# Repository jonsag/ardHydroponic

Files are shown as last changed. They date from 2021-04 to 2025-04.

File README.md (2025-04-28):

# ardHydroponic

An Arduino Mega managing a hydroponic plant bed.  

Visualization on an LCD screen  
Managed and configured with push buttons  
Data uploaded to Blynk app and ThingSpeak  
Monitored on a webpage

## Hardware

Things marked as optional are used when you make a PCB and/or an ESP-01 module.  

1 x Arduino Mega 2560, [AliExpress](https://www.aliexpress.com/wholesale?SearchText=arduino+mega+2560)  

1 x LCD display, 4x20 with I2C communication, [AliExpress](https://www.aliexpress.com/wholesale?SearchText=lcd+4x20+i2c)  

1 x ESP-01 module, [AliExpress](https://www.aliexpress.com/wholesale?SearchText=esp-01) (optional)  

5 x Momentary push button [AliExpress](https://www.aliexpress.com/wholesale?SearchText=switch+dip+6mm)  

5 x MOSFET module, [AliExpress](https://www.aliexpress.com/wholesale?SearchText=mosfet+module+irf520)  

4 x pump, [AliExpress](https://www.aliexpress.com/wholesale?SearchText=peristaltic+pump)  

1 x magnetic stirrer, [DIY suggestion](https://www.instructables.com/How-to-Make-a-Cheap-Portable-Magnetic-Stirrer/)  

1 x EC/TDS sensor, [AliExpress](https://www.aliexpress.com/wholesale?SearchText=dfrobot+gravity+tds)  

1 x pH sensor, [AliExpress](https://www.aliexpress.com/wholesale?SearchText=dfrobot+gravity+ph)  

1 x DS18B20 temperature sensor, [AliExpress](https://www.aliexpress.com/wholesale?SearchText=ds18b20)  

1 x KY-019 relay module, [AliExpress](https://www.aliexpress.com/wholesale?SearchText=ky-019) (optional)  

5 x 10 kohm resistor  

1 x 4.7 kohm resistor  

1 x 1 kohm resistor (optional)  

1 x 2.2 kohm resistor (optional)  

1 x 2 pole screw terminal block, 5.0mm leg space [AliExpress](https://www.aliexpress.com/wholesale?SearchText=screw+terminal+block+5.0+mm) (optional)  

1 x 3 pole screw terminal block, 5.0mm leg space [AliExpress](https://www.aliexpress.com/wholesale?SearchText=screw+terminal+block+5.0+mm) (optional)  

1 x 5 pole screw terminal block, 5.0mm leg space [AliExpress](https://www.aliexpress.com/wholesale?SearchText=screw+terminal+block+5.0+mm) (optional)  

1 x 6 pole screw terminal block, 5.0mm leg space [AliExpress](https://www.aliexpress.com/wholesale?SearchText=screw+terminal+block+5.0+mm) (optional)  

1 x 4x2 pin socket header (optional)  

Some single row pin and socket headers, 100mil legs space (optional)  

1 x DC power source, same voltage as your pumps. If this will also feed the Arduino board, not higher than 12V  

A PCB like the one in [this gerber zip](KiCAD/ardHydroponic/Gerber/ardHydroponic.zip) (optional)  

Connect and build everything according to the [schematics](KiCAD/ardHydroponic/ardHydroponic.pdf) in KiCAD.  

Calibration fluids:  
pH: two solutions with known values, for example 4.00 and 7.00  (other values will also work)  
TDS: solution with known TDS value  

## Usage

Your setup will have five push buttons and one LCD display.  
Everything is monitored and adjusted from the LCD.  
A lot of output is also provided on the serial output from the Mega.  

### Modes

There are four major modes of the system:  

* Running...  
* Maintenance  
* Settings  
* Special  

Also there is a 'Reading...' mode that the system enters when measuring in 'Running...' mode, and an 'Uploading...' mode when uploading data to internet.  

You advance from one mode to the next by pushing and holding down 'Button 1' for one second.  
When you do this in 'Special' mode you loop back to 'Running...' mode again.  

### 'Running...' mode

Button number:  

1. Enter next mode  
   * Long press: enter next mode  
2. No function  
3. No function  
4. No function  
5. No function  

LCD shows measured values, and whether they're too low or too high  

### 'Maintenance' mode

Button number:  

1. Enter next mode/Toggle output
   * Long press: enter next mode  
   * Short press: start or stop the indicated output  
2. Select previous output
3. Select next output
4. No function
5. No function

LCD shows selected output  

### 'Settings' mode

Button number:  

1. Enter next mode/Save variable  
   * Long press: leave this mode and enter next  
   * Short press: save variable to EEPROM  
2. Select previous variable
3. Select next variable
4. Step down selected variable
5. Step up selected variable

There are seventeen variables available:

* Nutr pump time,   ms
* pH+ pump time,    ms
* pH- pump time,    ms
* Clean pumps time, ms
* Iteration time,   ms
* Stir time,        ms
* Stir interval,    ms
* pH low,           pH
* pH high,          pH
* TDS low,         ppm
* k value,    constant
* TDS factor, constant
* Neutral pH,       pH
* Acid pH,          pH
* Neutral voltage,  mV
* Acid voltage,     mV
* pH voltage offs., mV

The names are pretty self explanatory.  
However, the last seven of these will be further explained in the calibration section below.  

The second line on the LCD will show the variable name.  
Line three will show the value stored in EEPROM.  
Line four will show the new value you step up and down.  

Also lines three and four will show pH and TDS when applicable.  

There is some sanity checking done of these variables when changing them via the LCD, but beware of what you tap in.  

### 'Special' mode

Button number:  

1. Enter next mode/Run action  
   * Long press: leave this mode and enter next  
   * Short press: Run selected action  
2. Select previous action
3. Select next action
4. No function
5. No function

LCD shows selected action and action result  

#### Actions

* Interact with ESP module in serial monitor
* Clear EEPROM. On next restart the EEPROM will be rewritten with the default values from config
* Reset ESP module
* Reset whole system
* Toggle the serial debugging output. Will go back to the setting in config.h after a restart.
* Print the IP of the ESP module
* Print MAC address of the ESP module

## Calibration

### TDS value

Put the TDS sensor in a solution with a know TDS value.  

Enter 'Settings' mode.

Select the 'TDS factor' variable using 'Button 2' and 'Button 3'.  
Enter the TDS factor of your known solution using 'Button 4' and 'Button 5'.  
The TDS value on the left of the screen will be updated whenever you push those buttons.  
Save the new 'TDS factor' with a short press on 'Button 1'.  

Select the 'k value' variable using 'Button 2' and 'Button 3'.  
Step up and down 'k value' using 'Button 4' and 'Button 5'.  
The TDS value on the left of the screen will be updated whenever you push those buttons.  
When the TDS value shown on screen correlates with your known solution save the 'k value' with a short press on 'Button 1'.  

### pH value

Enter 'Settings' mode.  

Select the 'Neutral pH' variable using 'Button 2' and 'Button 3'.  
Enter the pH value of your known solution, ie the one with the higher pH, using 'Button 4' and 'Button 5'.  
Save the new value with a short press on 'Button 1'.  

Select the 'Acid pH' variable using 'Button 2' and 'Button 3'.  
Enter the pH value of your known solution, ie the one with the lower pH, using 'Button 4' and 'Button 5'.  
Save the new value with a short press on 'Button 1'.  

Put your pH sensor in the neutral solution.  
Select the 'Neutral voltage' variable using 'Button 2' and 'Button 3'.  
On the lower right of the screen you will now see the measured voltage from the pH sensor in millivolts. You can't change that. However, pressing 'Button 4' or 'Button 5' will update that measurement.  
When you get a solid reading, save the value with a short press on 'Button 1'.  

Put your pH sensor in the acid solution.  
Select the 'Acid voltage' variable using 'Button 2' and 'Button 3'.  
On the lower right of the screen you will now see the measured voltage from the pH sensor in millivolts. You can't change that. However, pressing 'Button 4' or 'Button 5' will update that measurement.  
When you get a solid reading, save the value with a short press on 'Button 1'.  

There is also a 'pH voltage offset' for further trimming.  

## Web interface

A simple web page shows last data read and ThingSpeak upload status.  

You can also disable an enable the outputs relay from the page.

You can find the IP address of the web server using the 'Special' mode.  

## Blynk app

The app shows latest values of the sensors.  

Also you can control the outputs relay from it.  

## Software configuration

All configuration is made in 'config.h'

The most interesting variables are:

### varNames

If you want it in your own language, change it here.  
Other LCD output is mostly found in 'LCD.h', but also in some other places. Sorry...  

### vars

These are the start values of the variables that can be edited from the LCD.  
If you change these after having having uploaded the sketch once, it will not be used since these are now read from EEPROM.  

### incs

The increments/decrements of the variables above.  
(How big should the jumps be when using buttons 'Button 4' and 'Button5'.)  

## Libraries and boards in Arduino IDE

Most can be installed from within the Arduino IDE, but look out for the liquid crystal library so you don't install the wrong one.  
Read below!  

### ESP8266 board library

Add [http://arduino.esp8266.com/stable/package_esp8266com_index.json](http://arduino.esp8266.com/stable/package_esp8266com_index.json) (as a text line), in Files->Preferences->Additional Boards Manager URLs:  

Then go to Tools->Board:...->Boards Manager...,search for esp8266 and install it.  

### LiquidCrystal_I2C

Don't install the LiquidCrystal_I2C library with Arduino IDE's library manager.  

Instead use the one from [https://github.com/fdebrabander/Arduino-LiquidCrystal-I2C-library](https://github.com/fdebrabander/Arduino-LiquidCrystal-I2C-library).  

### FTDebouncer

[https://github.com/ubidefeo/FTDebouncer](https://github.com/ubidefeo/FTDebouncer)  

### Blynk

[https://github.com/blynkkk/blynk-library](https://github.com/blynkkk/blynk-library)  

### ThingSpeak

[https://github.com/iobridge/thingspeak](https://github.com/iobridge/thingspeak)  

### NTPClient

[https://github.com/arduino-libraries/NTPClient](https://github.com/arduino-libraries/NTPClient)  

## Install and configure

### Create accounts for online visualizations

#### thingspeak

Get an account at [thingspeak.com](https://thingspeak.com).

Create a new channel with the fields:

* Field1: Temp
* Field2: pH
* Field3: TDS

Take note of your channel ID and write API key.  

#### blynk

Download [Blynk](https://play.google.com/store/apps/details?id=cc.blynk) to your phone.  

Open Blynk and create a new project.  

Add widget boxes:  

* Gauge, Temperature, Input: Virtual V0, scaled 0-30
* Gauge, pH, Input: Virtual V1, scaled 0-15
* Gauge, TDS, Input Virtual V2, scaled 0-4000
* Button, Enabled, Mode: Switch, Output: Virtual V3

In your mail you will have received the authorization token.  

### Arduino Mega

Compile and upload hydroponicBase/src/* with, for example, Platform IO.  

When uploading over USB you must open up the connection between D14 and RESET, ie remove the jumper JP1.

### ESP-01

Rename/copy hydroponicConnect/src/secrets.h.template to hydroponicConnect/src/secrets.h, and edit it with your own values/keys.  

Compile and upload hydroponicConnect/src/* with, for example, Platform IO.  

## Trouble shooting

### Resetting EEPROM to default values at every start

Edit ardHydroponic.ino  

Uncomment the line  

    //clearEEPROM();

and upload sketch.  

## Misc

### Useful programs

#### cu

A simple serial monitor  

Get serial output  
>$ cu -l /dev/ttyACM0 -s 9600

Exit with ~. (tilde dot)  

#### picocom

A more versatile serial monitor  

Get serial output  
>$ picocom -b 115200 /dev/ttyACM0 --omap crcrlf

Exit with Ctrl+a Ctrl+x  

### Links

EC sensor:  
[https://wiki.dfrobot.com/Gravity__Analog_TDS_Sensor___Meter_For_Arduino_SKU__SEN0244](https://wiki.dfrobot.com/Gravity__Analog_TDS_Sensor___Meter_For_Arduino_SKU__SEN0244)  

pH sensor:  
[https://wiki.dfrobot.com/Gravity__Analog_pH_Sensor_Meter_Kit_V2_SKU_SEN0161-V2](https://wiki.dfrobot.com/Gravity__Analog_pH_Sensor_Meter_Kit_V2_SKU_SEN0161-V2)  

### Screen shots

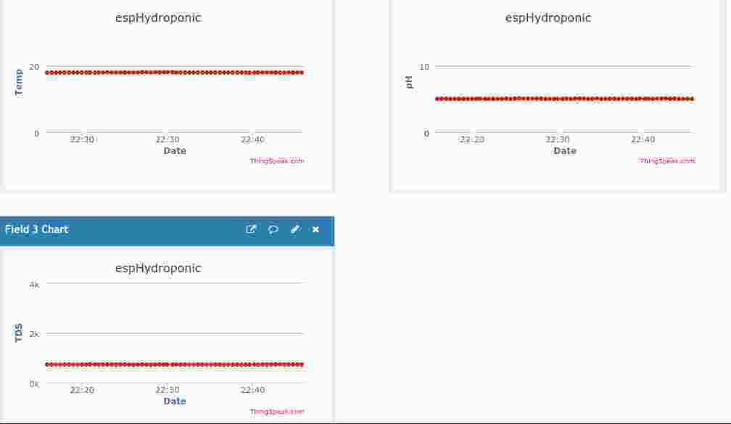
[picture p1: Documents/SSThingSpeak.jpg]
ThingSpeak
  
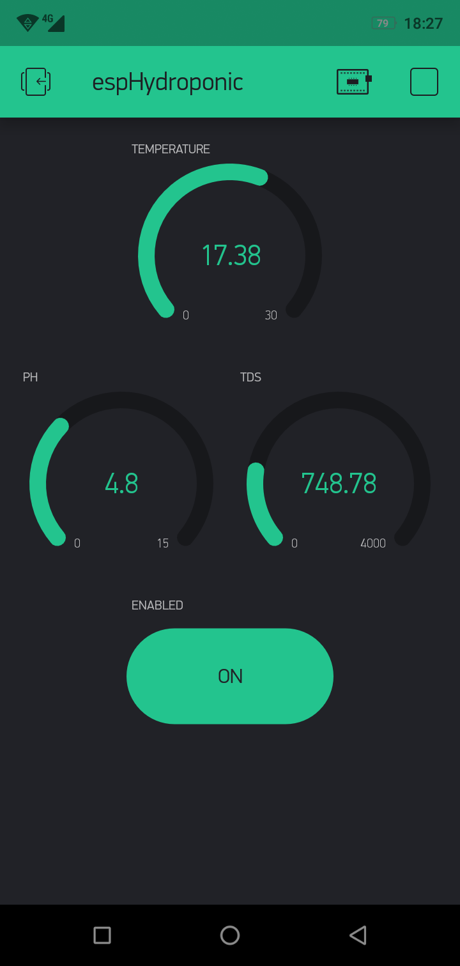
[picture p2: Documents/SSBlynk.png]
Blynk
  
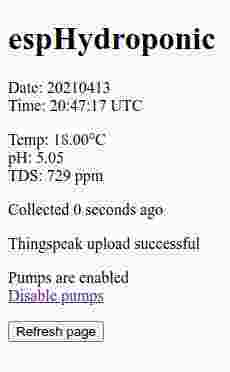
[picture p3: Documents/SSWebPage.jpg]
Web interface


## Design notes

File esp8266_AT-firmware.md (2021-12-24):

# espLogger

An ESP-01 module to handle logging and monitoring of the ardHydroponic.  

## Check firmware version

Hook up your FTDI device to the ESP module.  

    FTDI            ESP-01  
    1 GND   ->      2   GND
    2 CTS   ->
    3 VCC   ->      7   VCC
    4 Tx    ->      8   Rx
    5 Rx    ->      1   Tx
    6 DTR   ->

Check connection with picocom  
>$ picocom -b 115200 /dev/ttyUSB0 --omap crcrlf  

    picocom v2.2

    port is        : /dev/ttyUSB0
    flowcontrol    : none
    baudrate is    : 115200
    parity is      : none
    databits are   : 8
    stopbits are   : 1
    escape is      : C-a
    local echo is  : no
    noinit is      : no
    noreset is     : no
    nolock is      : no
    send_cmd is    : sz -vv
    receive_cmd is : rz -vv -E
    imap is        : 
    omap is        : crcrlf,
    emap is        : crcrlf,delbs,

    Type [C-a] [C-h] to see available commands

    Terminal ready

Check if the ESP is answering  
>AT

    OK  

Check fw version  
>AT+GMR

    AT version:0.25.0.0(Jun  5 2015 16:27:16)
    SDK version:1.1.1
    Ai-Thinker Technology Co. Ltd.
    Jun 23 2015 23:23:50

    OK

Exit program  
>$ Ctrl+a Ctrl+x  

## Update firmware

Install tool  
>$ pip install esptool

Pull GPIO0 to ground and start the ESP via the FTDI.  
Also make sure you got a solid 3.3V source as the chip will not boot properly otherwise.  

### Source from aprbrother  

Download firmware from [http://wiki.aprbrother.com/wiki/Firmware_For_ESP8266](http://wiki.aprbrother.com/wiki/Firmware_For_ESP8266).  
>$ wget https://i1.aprbrother.com/ai-thinker-v1.1.1.bin  

Flash firmware  
>$ esptool.py -p /dev/ttyUSB0 -b 115000 write_flash 0x000000 ai-thinker-v1.1.1.bin  

    esptool.py v3.0
    Serial port /dev/ttyUSB0
    Connecting....
    Detecting chip type... ESP8266
    Chip is ESP8266EX
    Features: WiFi
    Crystal is 26MHz
    MAC: e8:db:84:dc:4e:77
    Uploading stub...
    Running stub...
    Stub running...
    Configuring flash size...
    Compressed 1044480 bytes to 204643...
    Wrote 1044480 bytes (204643 compressed) at 0x00000000 in 18.2 seconds (effective 459.2 kbit/s)...
    Hash of data verified.

    Leaving...
    Hard resetting via RTS pin...

### Get AT sources from EspressIF

[https://www.espressif.com/en/support/download/at?keys=&field_type_tid%5B%5D=799](https://www.espressif.com/en/support/download/at?keys=&field_type_tid%5B%5D=799)  

Look for ESP8266 NonOS AT Bin, download and extract it  

### Source from espressif, ESP8266 NonOS AT Bin v1.7.4  
  
>$ wget https://www.espressif.com/sites/default/files/ap/ESP8266_NonOS_AT_Bin_V1.7.4.zip  
>$ unzip ESP8266_NonOS_AT_Bin_V1.7.4.zip  
>$ cd ESP8266_NonOS_AT_Bin_V1.7.4/bin/  

Find out how to upload it  
>$ cat at/README.md

    ...
    ### Flash size 8Mbit: 512KB+512KB
        boot_v1.2+.bin              0x00000
        user1.1024.new.2.bin        0x01000
        esp_init_data_default.bin   0xfc000
        blank.bin                   0x7e000 & 0xfe000
    ...

Flash chip  
>$ esptool.py -p /dev/ttyUSB0 -b 74880 write_flash --flash_size 1MB --flash_freq 26m 0x00000 boot_v1.7.bin 0x01000 at/512+512/user1.1024.new.2.bin 0xFC000 esp_init_data_default_v08.bin 0x7E000 blank.bin 0xFE000 blank.bin

Or with fewer options  
>$ esptool.py -p /dev/ttyUSB0 write_flash 0x00000 boot_v1.7.bin 0x01000 at/512+512/user1.1024.new.2.bin 0xFC000 esp_init_data_default_v08.bin 0x7E000 blank.bin 0xFE000 blank.bin  

    esptool.py v3.0
    Serial port /dev/ttyUSB0
    Connecting....
    Detecting chip type... ESP8266
    Chip is ESP8266EX
    Features: WiFi
    Crystal is 26MHz
    MAC: e8:db:84:dc:4e:77
    Uploading stub...
    Running stub...
    Stub running...
    Configuring flash size...
    Compressed 4080 bytes to 2936...
    Wrote 4080 bytes (2936 compressed) at 0x00000000 in 0.4 seconds (effective 78.4 kbit/s)...
    Hash of data verified.
    Compressed 413444 bytes to 296966...
    Wrote 413444 bytes (296966 compressed) at 0x00001000 in 40.4 seconds (effective 81.8 kbit/s)...
    Hash of data verified.
    Compressed 128 bytes to 75...
    Wrote 128 bytes (75 compressed) at 0x000fc000 in 0.0 seconds (effective 32.0 kbit/s)...
    Hash of data verified.
    Compressed 4096 bytes to 26...
    Wrote 4096 bytes (26 compressed) at 0x0007e000 in 0.0 seconds (effective 2052.6 kbit/s)...
    Hash of data verified.
    Compressed 4096 bytes to 26...
    Wrote 4096 bytes (26 compressed) at 0x000fe000 in 0.0 seconds (effective 2034.8 kbit/s)...
    Hash of data verified.

    Leaving...
    Hard resetting via RTS pin...

Firmware check in serial monitor  
>AT+GMR

    AT version:1.7.4.0(May 11 2020 19:13:04)
    SDK version:3.0.4(9532ceb)
    compile time:May 27 2020 10:12:17
    Bin version(Wroom 02):1.7.4
    OK

### Source from espressif, ESP8266 NonOS AT Bin v1.6.2  

Get source  
>$ wget wget https://www.espressif.com/sites/default/files/ap/ESP8266_AT_Bin_V1.6.2_0.zip  
>$ unzip ESP8266_AT_Bin_V1.6.2_0.zip  
>$ cd ESP8266_AT_Bin_V1.6.2/bin/  

Find out how to upload it  
>$ cat at/README.md

    ...
    ### Flash size 8Mbit: 512KB+512KB
        boot_v1.2+.bin              0x00000
        user1.1024.new.2.bin        0x01000
        esp_init_data_default.bin   0xfc000 (optional)
        blank.bin                   0x7e000 & 0xfe000
    ...

Flash chip  
>$ esptool.py -p /dev/ttyUSB0 -b 74880 write_flash --flash_size 1MB --flash_freq 26m 0x00000 boot_v1.7.bin 0x01000 at/512+512/user1.1024.new.2.bin 0xFC000 esp_init_data_default_v08.bin 0x7E000 blank.bin 0xFE000 blank.bin

    esptool.py v3.0
    Serial port /dev/ttyUSB0
    Connecting....
    Detecting chip type... ESP8266
    Chip is ESP8266EX
    Features: WiFi
    Crystal is 26MHz
    MAC: e8:db:84:dc:4e:77
    Uploading stub...
    Running stub...
    Stub running...
    Configuring flash size...
    Compressed 4080 bytes to 2936...
    Wrote 4080 bytes (2936 compressed) at 0x00000000 in 0.4 seconds (effective 78.3 kbit/s)...
    Hash of data verified.
    Compressed 408388 bytes to 293527...
    Wrote 408388 bytes (293527 compressed) at 0x00001000 in 40.1 seconds (effective 81.5 kbit/s)...
    Hash of data verified.
    Compressed 128 bytes to 75...
    Wrote 128 bytes (75 compressed) at 0x000fc000 in 0.0 seconds (effective 32.6 kbit/s)...
    Hash of data verified.
    Compressed 4096 bytes to 26...
    Wrote 4096 bytes (26 compressed) at 0x0007e000 in 0.0 seconds (effective 2048.4 kbit/s)...
    Hash of data verified.
    Compressed 4096 bytes to 26...
    Wrote 4096 bytes (26 compressed) at 0x000fe000 in 0.0 seconds (effective 2175.0 kbit/s)...
    Hash of data verified.

    Leaving...
    Hard resetting via RTS pin...

Firmware check in serial monitor  
>AT+GMR

    AT version:1.6.2.0(Apr 13 2018 11:10:59)
    SDK version:2.2.1(6ab97e9)
    compile time:Jun  7 2018 19:34:26
    Bin version(Wroom 02):1.6.2
    OK

### Source from espressif, ESP8266 NonOS AT Bin v1.5.1  

Get source  
>$ wget wget https://www.espressif.com/sites/default/files/ap/esp8266_at_bin_v1.5.1.zip  
>$ unzip esp8266_at_bin_v1.5.1.zip  
>$ cd ESP8266_AT_Bin_V1.5.1/bin  

Find out how to upload it  
>$ cat at/README.md

    ...
    ### Flash size 8Mbit: 512KB+512KB
        boot_v1.2+.bin              0x00000
        user1.1024.new.2.bin        0x01000
        esp_init_data_default.bin   0xfc000 (optional)
        blank.bin                   0x7e000 & 0xfe000
    ...

Flash chip  
>$ esptool.py -p /dev/ttyUSB0 -b 74880 write_flash --flash_size 1MB --flash_freq 26m 0x00000 boot_v1.7.bin 0x01000 at/512+512/user1.1024.new.2.bin 0xfc000 esp_init_data_default.bin 0x7E000 blank.bin 0xFE000 blank.bin

    esptool.py v3.0
    Serial port /dev/ttyUSB0
    Connecting....
    Detecting chip type... ESP8266
    Chip is ESP8266EX
    Features: WiFi
    Crystal is 26MHz
    MAC: e8:db:84:dc:4e:77
    Uploading stub...
    Running stub...
    Stub running...
    Configuring flash size...
    Compressed 4080 bytes to 2936...
    Wrote 4080 bytes (2936 compressed) at 0x00000000 in 0.4 seconds (effective 78.3 kbit/s)...
    Hash of data verified.
    Compressed 427044 bytes to 305765...
    Wrote 427044 bytes (305765 compressed) at 0x00001000 in 41.6 seconds (effective 82.1 kbit/s)...
    Hash of data verified.
    Compressed 128 bytes to 75...
    Wrote 128 bytes (75 compressed) at 0x000fc000 in 0.0 seconds (effective 32.0 kbit/s)...
    Hash of data verified.
    Compressed 4096 bytes to 26...
    Wrote 4096 bytes (26 compressed) at 0x0007e000 in 0.0 seconds (effective 2153.5 kbit/s)...
    Hash of data verified.
    Compressed 4096 bytes to 26...
    Wrote 4096 bytes (26 compressed) at 0x000fe000 in 0.0 seconds (effective 2133.6 kbit/s)...
    Hash of data verified.

    Leaving...
    Hard resetting via RTS pin...

Firmware check in serial monitor  
>AT+GMR

    AT version:1.5.0.0(Oct 24 2017 12:03:18)
    SDK version:2.1.0(ace2d95)
    compile time:Oct 24 2017 15:48:02
    Bin version(Wroom 02):1.5.1
    OK

### After upload

Remove the ground connection on GPIO0 and boot up and connect again  
>$ picocom -b 115200 /dev/ttyUSB0 --omap crcrlf  

## AT commands

Check firmware version  
>AT+GMR  

    AT version:1.3.0.0(Jul 14 2016 18:54:01)
    SDK version:2.0.0(5a875ba)
    v1.0.0.3
    Mar 13 2018 09:35:47
    OK

Check WiFi mode  
>AT+CWMODE?  

    +CWMODE:0

    OK

Set as station  
>AT+CWMODE=1

    OK

Mode 1 -> STA (station)  
Mode 2 -> AP (access point)  
Mode 3 -> Both

Search for access points  
>AT+CWLAP

    +CWLAP:(0,"ESP-E0569F",-56,"52:02:91:e0:56:9f",11)
    +CWLAP:(2,"tureborg2",-55,"00:1b:2f:50:e6:16",11)

    OK

Connect to access point  
>AT+CWJAP="\<access point>","\<password>"  

    WIFI CONNECTED
    WIFI GOT IP

    OK

Show IP-address
>AT+CIFSR

    +CIFSR:APIP,"192.168.4.1"
    +CIFSR:APMAC,"ea:db:84:dc:4e:77"
    +CIFSR:STAIP,"192.168.10.78"
    +CIFSR:STAMAC,"e8:db:84:dc:4e:77"

    OK

Disconnect from access point
>AT+CWQAP

    WIFI DISCONNECT

    OK

Set serial speed  
>AT+CIOBAUD=9600

    OK

Permanently set serial speed, for example, 9600 baud / 8 data bits / 1 stop bits and none parity and flow control  
>AT+UART_DEF=9600,8,1,0,0

Reset  
>AT+RST

    OK
    WIFI DISCONNECT
    ...
    Ai-Thinker Technology Co. Ltd.

    invalid
    WIFI CONNECTED
    WIFI GOT IP

## esptool.py

When using esptool you must pull GPIO0 to GND  

Allowed baud rates:  
74880, 115200, 230400, 460800, 921600, 1500000, >1500000

Read MAC address  
>$ esptool.py -p /dev/ttyUSB0 read_mac

    esptool.py v3.0
    Serial port /dev/ttyUSB0
    Connecting....
    Detecting chip type... ESP8266
    Chip is ESP8266EX
    Features: WiFi
    Crystal is 26MHz
    MAC: e8:db:84:dc:4e:77
    Uploading stub...
    Running stub...
    Stub running...
    MAC: e8:db:84:dc:4e:77
    Hard resetting via RTS pin...

Find flash size  
>$ esptool.py -p /dev/ttyUSB0 flash_id

    esptool.py v3.0
    Serial port /dev/ttyUSB0
    Connecting....
    Detecting chip type... ESP8266
    Chip is ESP8266EX
    Features: WiFi
    Crystal is 26MHz
    MAC: e8:db:84:dc:4e:77
    Uploading stub...
    Running stub...
    Stub running...
    Manufacturer: 20
    Device: 4014
    Detected flash size: 1MB
    Hard resetting via RTS pin...

Erase flash  
>$ esptool.py -p /dev/ttyUSB0 erase_flash

    esptool.py v3.0
    Serial port /dev/ttyUSB0
    Connecting....
    Detecting chip type... ESP8266
    Chip is ESP8266EX
    Features: WiFi
    Crystal is 26MHz
    MAC: e8:db:84:dc:4e:77
    Uploading stub...
    Running stub...
    Stub running...
    Erasing flash (this may take a while)...
    Chip erase completed successfully in 4.1s
    Hard resetting via RTS pin...

Create a merged .bin  
>$ esptool.py --chip esp8266 merge_bin -o merged-flash.bin --flash_mode dio --flash_size 1MB 0x00000 boot_v1.7.bin 0x01000 at/512+512/user1.1024.new.2.bin 0xFC000 esp_init_data_default_v08.bin 0x7E000 blank.bin 0xFE000 blank.bin

Upload merged .bin  
>$ esptool.py -p /dev/ttyUSB0 -b 115000 write_flash 0x0 merged-flash.bin

Verify upload
>$ esptool.py -p /dev/ttyUSB0 -b 74880 verify_flash --diff yes 0x00000 boot_v1.7.bin 0x01000 at/512+512/user1.1024.new.2.bin 0xfc000 esp_init_data_default_v08.bin 0x7e000 blank.bin 0xfe000 blank.bin

## picocom

Allowed baud rates:  
300, 600, 1200, 2400, 4800, 9600, 19200, 38400, 57600, 115200  

Connect
>$ picocom -b 115200 /dev/ttyUSB0 --omap crcrlf  

View help  
> [Ctrl+a][Ctrl+h]  

Quit  
> [Ctrl+a][Ctrl+q]  

## Links

Espressif AT firmware:  
[https://www.espressif.com/en/support/download/at](https://www.espressif.com/en/support/download/at)  

AT instruction set  
[https://www.espressif.com/sites/default/files/documentation/4a-esp8266_at_instruction_set_en.pdf](https://www.espressif.com/sites/default/files/documentation/4a-esp8266_at_instruction_set_en.pdf)  

[https://docs.linuxconsulting.mn.it/esp8266/firmware-programming](https://docs.linuxconsulting.mn.it/esp8266/firmware-programming)  
[https://www.espressif.com/en/products/socs/esp8266ex/resources](https://www.espressif.com/en/products/socs/esp8266ex/resources)

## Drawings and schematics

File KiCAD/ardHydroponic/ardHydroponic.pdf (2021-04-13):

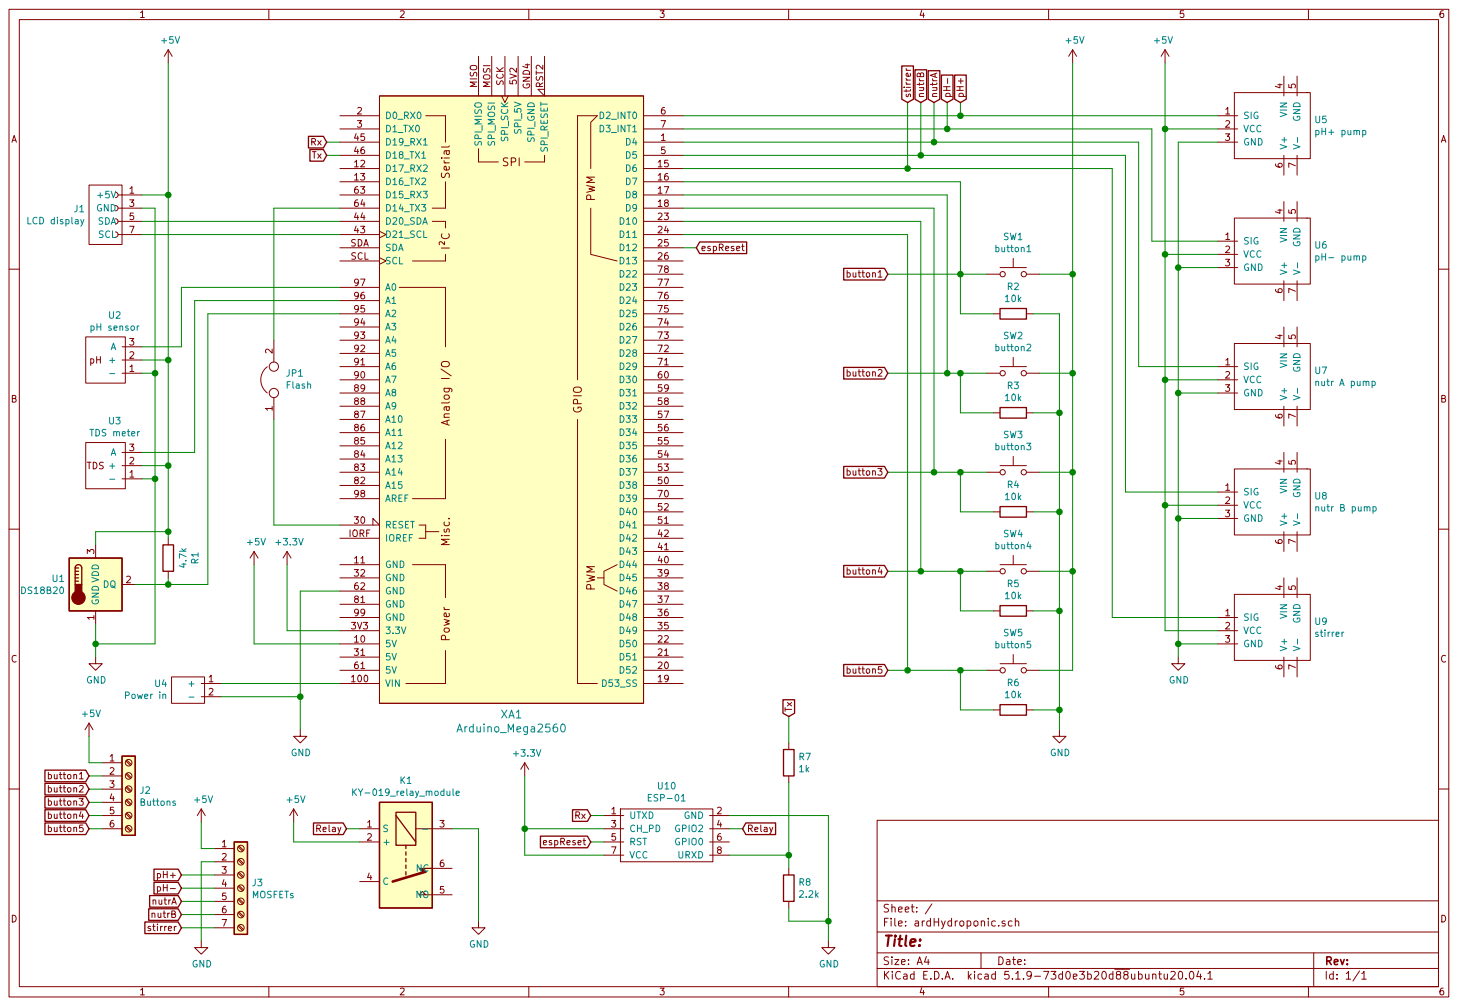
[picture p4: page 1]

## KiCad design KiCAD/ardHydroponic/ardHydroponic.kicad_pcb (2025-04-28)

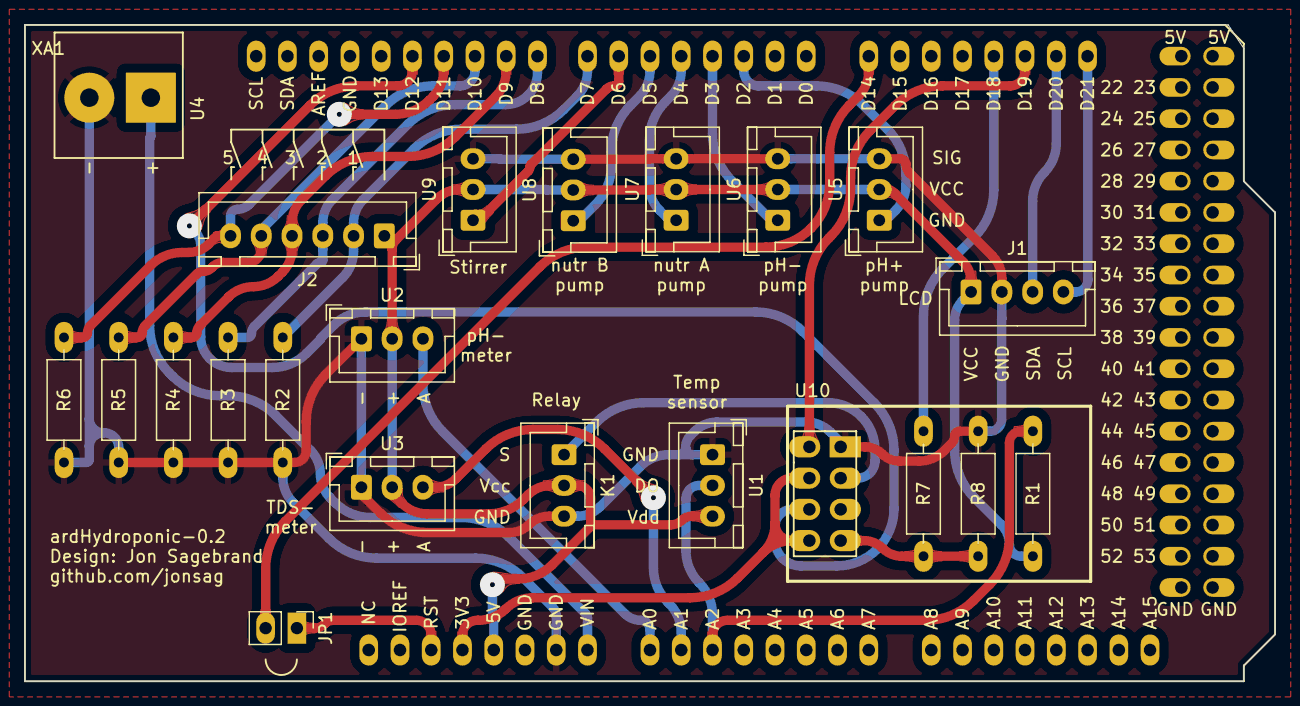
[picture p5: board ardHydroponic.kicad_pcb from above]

Board: 2 copper layers, 101.6 x 53.3 mm, 23 parts (0 on the bottom side), 26 nets.

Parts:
J1: LCD 4x20; 4-pin JST LCD
J2: Buttons; 6-pin JST 5-buttons
JP1: Flash; Jumper_1x02_P2.54mm_large
K1: KY-019_relay_module; 3-pin JST KY-019 relay
R1: 4.7k; R_Axial_DIN0207_L6.3mm_D2.5mm_P10.16mm_Horizontal_larger_pa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
R2, R3, R4, R5, R6: 10k; R_Axial_DIN0207_L6.3mm_D2.5mm_P10.16mm_Horizontal_larger_pa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
R7: 1k; R_Axial_DIN0207_L6.3mm_D2.5mm_P10.16mm_Horizontal_larger_pa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
R8: 2.2k; R_Axial_DIN0207_L6.3mm_D2.5mm_P10.16mm_Horizontal_larger_pa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
U1: DS18B20; 3-pin JST DS18B20
U2: pH sensor; 3-pin JST pH Sensor
U3: TDS meter; 3-pin JST TDS Meter
U4: Power in; 2-pole_power_in_screw_terminal
U5: pH+ pump; 3-pin JST IRF520 MOSFET module
U6: pH- pump; 3-pin JST IRF520 MOSFET module
U7: nutr A pump; 3-pin JST IRF520 MOSFET module
U8: nutr B pump; 3-pin JST IRF520 MOSFET module
U9: stirrer; 3-pin JST IRF520 MOSFET module
U10: ESP-01; ESP-01_w_pin_socket_large
XA1: Arduino_Mega2560; Arduino_Mega2560_Shield__no_ICSP_no_mount-holes_large

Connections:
+3V3: U10.4 (CH_PD/CH_EN), U10.8 (VCC), XA1.3V3 (3.3V)
+5V: J1.1 (+5V), J2.1, K1.2 (+), R1.2, U1.3 (VDD), U2.2 (+), U3.2 (+), U5.2 (VCC), U6.2 (VCC), U7.2 (VCC), U8.2 (VCC), U9.2 (VCC), XA1.10 (5V)
GND: J1.2 (GND), K1.3 (-), R2.1, R3.1, R4.1, R5.1, R6.1, R8.2, U1.1 (GND), U2.1 (-), U3.1 (-), U4.2 (-), U5.3 (GND), U6.3 (GND), U7.3 (GND), U8.3 (GND), U9.3 (GND), U10.1 (GND), XA1.62 (GND)
unnamed: JP1.1 (A), XA1.30 (RESET)
unnamed: JP1.2 (B), XA1.64 (D14_TX3)
unnamed: R1.1, U1.2 (DQ), XA1.95 (A2)
unnamed: R7.2, R8.1, U10.7 (GPIO3/UORxD)
unnamed: U2.3 (A), XA1.97 (A0)
unnamed: U3.3 (A), XA1.96 (A1)
unnamed: U4.1 (+), XA1.100 (VIN)
unnamed: J1.4 (SCL), XA1.43 (D21_SCL)
unnamed: J1.3 (SDA), XA1.44 (D20_SDA)
Relay: K1.1 (S), U10.3 (GPIO2)
Rx: U10.2 (GPIO1/UOTxD), XA1.45 (D19_RX1)
Tx: R7.1, XA1.46 (D18_TX1)
button1: J2.2, R2.2, XA1.16 (D7)
button2: J2.3, R3.2, XA1.17 (D8)
button3: J2.4, R4.2, XA1.18 (D9)
button4: J2.5, R5.2, XA1.23 (D10)
button5: J2.6, R6.2, XA1.24 (D11)
espReset: U10.6 (Reset), XA1.25 (D12)
nutrA: U7.1 (SIG), XA1.1 (D4)
nutrB: U8.1 (SIG), XA1.5 (D5)
pH+: U5.1 (SIG), XA1.6 (D2_INT0)
pH-: U6.1 (SIG), XA1.7 (D3_INT1)
stirrer: U9.1 (SIG), XA1.15 (D6)

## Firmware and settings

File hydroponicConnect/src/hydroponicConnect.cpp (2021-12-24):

//#define DODEBUG // uncomment this for debugging output

/**********
 * Debug
 **********/
#ifdef DODEBUG
#define BLYNK_DEBUG
#define BLYNK_PRINT Serial
bool debug = 1;
#include "user_interface.h"
#else
bool debug = 0;
#endif

/**********
 * Includes
 **********/
#include <Arduino.h>
#include <ESP8266WiFi.h>
#include <WiFiClient.h>
#include <ESP8266WebServer.h>
//#include <ESP8266mDNS.h>
#include <NTPClient.h>
#include <WiFiUdp.h>
#include <BlynkSimpleEsp8266.h>

#include "secrets.h"

#include "ThingSpeak.h"

/**********
 * WiFi
 **********/
const char *ssid = STASSID;
const char *password = STAPSK;
WiFiClient client;

/**********
 * ThingSpeak
 **********/
unsigned long myChannelNumber = channelID;
const char *myWriteAPIKey = apiKey;

/**********
 * UDP for ntp
 **********/
WiFiUDP ntpUDP;
const long utcOffsetInSeconds = 0; // 28800;
NTPClient timeClient(ntpUDP, "pool.ntp.org", utcOffsetInSeconds);

/**********
 * Times
 **********/
String formattedTime;
String Date;
int Day;
int Month;
int Year;

/**********
 * Messages from serial
 **********/
String message;

/**********
 * Values
 **********/
float temperatureSum = 0.0;
float pHValue = 0.0;
float tdsValue = 0.0;

/**********
 * Web server
 **********/
ESP8266WebServer server(80);

/**********
 * Outputs
 **********/
const byte relay = 2;
boolean relayState = HIGH;

/**********
 * Blynk
 **********/
char *blynkAuth = blynkToken;
int valueV3;
boolean lastValueV3 = HIGH;

BLYNK_WRITE(V3)
{
  valueV3 = param.asInt(); // Get value as integer
  if (valueV3)
  {
    relayState = HIGH;
  }
  else
  {
    relayState = LOW;
  }
  digitalWrite(relay, relayState);
}

/**********
 * Functions
 **********/
void handle_OnConnect();
void handle_NotFound();
void handle_toggleRelay();
void decodeMessage(String message);
String SendHTML(float temperatureSum, float pHValue, float tdsValueString, String TimeWeb, String DateWeb, unsigned long epochTime, unsigned long uploadedEpoch, boolean uploadSuccess, boolean relayState);
const char *wifi_status_to_string(wl_status_t status);
const char *wifi_station_get_connect_status_to_string(int status);

/**********
 * Misc
 **********/
boolean uploadSuccess = 0;

unsigned long uploadedEpoch;

void setup(void)
{
  /**********
   * Serial
   **********/
  Serial.setTimeout(10);
  Serial.begin(9600);
  if (debug)
    Serial.println("Serial started");

  /**********
   * WiFi mode
   **********/
  if (debug)
    Serial.println("Setting WiFi mode...");
  WiFi.mode(WIFI_STA);

  /**********
   * Scan for available networks
   **********/
  if (debug)
  { // https://arduino-esp8266.readthedocs.io/en/latest/esp8266wifi/scan-examples.html
    WiFi.disconnect();
    while (true)
    {
      Serial.println("Scanning for available networks...");
      delay(100);
      int n = WiFi.scanNetworks();
      if (n > 0)
      {
        Serial.print("Found ");
        Serial.print(n);
        if (n > 1)
        {
          Serial.println(" networks: ");
        }
        else
        {
          Serial.println(" network: ");
        }
        for (int i = 0; i < n; i++)
        {
          // Serial.println(WiFi.SSID(i));
          Serial.printf("%d: %s, Ch:%d (%ddBm) %s\n", i + 1, WiFi.SSID(i).c_str(), WiFi.channel(i), WiFi.RSSI(i), WiFi.encryptionType(i) == ENC_TYPE_NONE ? "open" : "");
        }
        break;
      }
      else
      {
        Serial.println("Didn't find any networks");
        Serial.println("You've got a problem!");
        Serial.println("Trying again in five seconds...");
        delay(5000);
      }
    }
  }

  /**********
   * ThingSpeak
   **********/
  if (debug)
    Serial.println("Starting ThingSpeak client...");
  ThingSpeak.begin(client); // Initialize ThingSpeak

  /**********
   * Webserver
   **********/
  if (debug)
    Serial.println("Configuring web server...");
  server.on("/", handle_OnConnect);
  server.onNotFound(handle_NotFound);
  server.on("/toggleRelay", handle_toggleRelay);
  server.begin();

  if (debug)
    Serial.println("HTTP server started");
  /**********
   * ntp
   **********/
  if (debug)
    Serial.println("Starting ntp client...");
  timeClient.begin();

  /**********
   * Outputs
   **********/
  if (debug)
    Serial.println("Starting outputs...");
  pinMode(relay, OUTPUT);
  digitalWrite(relay, relayState);

  /**********
   * WiFi connect
   **********/
  if (WiFi.status() != WL_CONNECTED)
  { // connect or reconnect to WiFi
    Serial.print("Attempting to connect to SSID: '");
    Serial.print(ssid);
    Serial.println("'");
    if (debug)
      Serial.print("Password: '");
    if (debug)
      Serial.print(password);
    if (debug)
      Serial.println("'");

    // WiFi.begin(ssid, password); // connect to WPA/WPA2 network
    WiFi.begin(ssid, password); // connect to WPA/WPA2 network

    while (WiFi.status() != WL_CONNECTED)
    {
#ifdef DODEBUG
      Serial.print("WiFi status: ");
      Serial.print(WiFi.status());
      Serial.print(", ");
      Serial.print(wifi_status_to_string(WiFi.status()));

      Serial.print("\t\tWiFi station connect status: ");
      Serial.print(wifi_station_get_connect_status());
      Serial.print(", ");
      Serial.println(wifi_station_get_connect_status_to_string(wifi_station_get_connect_status()));
#else
      Serial.print(".");
#endif
      delay(500);
    }
  }

#ifdef DODEBUG
  Serial.print("WiFi status: ");
  Serial.print(WiFi.status());
  Serial.print(", ");
  Serial.print(wifi_status_to_string(WiFi.status()));

  Serial.print("\t\tWiFi station connect status: ");
  Serial.print(wifi_station_get_connect_status());
  Serial.print(", ");
  Serial.println(wifi_station_get_connect_status_to_string(wifi_station_get_connect_status()));
#endif

  Serial.print("\nConnected with IP: ");
  Serial.println(WiFi.localIP());
  if (debug)
    Serial.println();

  /**********
   * Blynk
   **********/
  if (debug)
    Serial.println("Starting blynk...");

  Blynk.begin(blynkAuth, ssid, password);

  if (debug)
    Serial.println("All started");
}

void loop(void)
{
  if (WiFi.status() != WL_CONNECTED)
  { // connect or reconnect to WiFi
    Serial.println("Lost WiFi");
    Serial.print("Attempting to reconnect to SSID: ");
    Serial.println(ssid);
    WiFi.begin(ssid, password); // connect to WPA/WPA2 network
    while (WiFi.status() != WL_CONNECTED)
    {

      Serial.print(".");
      delay(500);
    }
    Serial.println("\nConnected.");
  }

  Blynk.run();

  server.handleClient();
  // MDNS.update();

  message = "";

  while (Serial.available())
  {
    // read the incoming byte:
    message = Serial.readString();

    decodeMessage(message);
  }
}

void handle_OnConnect()
{

  timeClient.update();

  unsigned long epochTime = timeClient.getEpochTime();
  String formattedTime = timeClient.getFormattedTime();

  struct tm *ptm = gmtime((time_t *)&epochTime);
  while (Serial1.available())
  {
    Serial.write(Serial1.read());
  }
  int monthDay = ptm->tm_mday;
  int currentMonth = ptm->tm_mon + 1;
  int currentYear = ptm->tm_year + 1900;

  Date = String(currentYear);
  if (currentMonth < 10)
  {
    Date += "0";
  }
  Date += String(currentMonth);
  if (monthDay < 10)
  {
    Date += "0";
  }
  Date += String(monthDay);

  server.send(200, "text/html", SendHTML(temperatureSum, pHValue, tdsValue, formattedTime, Date, epochTime, uploadedEpoch, uploadSuccess, relayState));
}

void handle_NotFound()
{
  String message404 = "File Not Found\n\n";
  message404 += "URI: ";
  message404 += server.uri();
  message404 += "\nMethod: ";
  message404 += (server.method() == HTTP_GET) ? "GET" : "POST";
  message404 += "\nArguments: ";
  message404 += server.args();
  message404 += "\n";
  for (uint8_t i = 0; i < server.args(); i++)
  {
    message404 += " " + server.argName(i) + ": " + server.arg(i) + "\n";
  }
  server.send(404, "text/plain", message404);
}

void handle_toggleRelay()
{
  if (relayState)
  {
    relayState = LOW;
  }
  else
  {
    relayState = HIGH;
  }

  digitalWrite(relay, relayState);
  Blynk.virtualWrite(V3, relayState);

  String togglePage = "<!DOCTYPE html>\n<html>\n";
  togglePage += "<head><meta name = \"viewport\" content=\"width=device-width, initial-scale=1.0, user-scalable=no\">\n"; // head
  togglePage += "<title>ESP8266 espHydroponic</title>\n";
  togglePage += "</head>\n";

  togglePage += "<body>\n"; // body
  togglePage += "<div id=\"webpage\">\n";

  togglePage += "<h1>espHydroponic</h1>\n";

  if (relayState)
  {
    togglePage += "<p>Pumps enabled</p>";
  }
  else
  {
    togglePage += "<p>Pumps disabled</p>";
  }

  togglePage += "<br>\n<button onclick = \"goBack()\">Go Back </button>\n";
  togglePage += "<script>\n";
  togglePage += "function goBack() {\n";
  togglePage += "window.history.back();\n";
  togglePage += "}\n";
  togglePage += "</script>\n";

  togglePage += "<p>Don't forget to refresh page once there</p>\n";

  togglePage += "</div>\n";
  togglePage += "</body>\n";
  togglePage += "</html>\n";

  server.send(200, "text / html", togglePage);
  // handle_OnConnect();
}

String SendHTML(float temperatureSum, float pHValue, float tdsValueString, String TimeWeb, String DateWeb, unsigned long epochTime, unsigned long uploadedEpoch, boolean uploadSuccess, boolean relayState)
{
  String mainPage = "<!DOCTYPE html>\n<html>\n";
  mainPage += "<head><meta name = \"viewport\" content=\"width=device-width, initial-scale=1.0, user-scalable=no\">\n"; // head
  mainPage += "<title>ESP8266 espHydroponic</title>\n";
  mainPage += "</head>\n";

  mainPage += "<body>\n"; // body
  mainPage += "<div id=\"webpage\">\n";

  mainPage += "<h1>espHydroponic</h1>\n"; // header

  mainPage += "<p>Date: "; // time and date
  mainPage += (String)DateWeb;
  mainPage += "\n";
  mainPage += "<br>Time: ";
  mainPage += (String)TimeWeb;
  mainPage += " UTC\n";

  if (debug)
  {
    mainPage += "<br>Epoch: ";
    mainPage += epochTime;
    Blynk.virtualWrite(V2, tdsValue);
  }
  mainPage += "</p>\n";

  mainPage += "<p>Temp: "; // values
  mainPage += temperatureSum;
  mainPage += "&#176;C\n";
  mainPage += "<br>pH: ";
  mainPage += pHValue;
  mainPage += "\n";
  mainPage += "<br>TDS: ";
  mainPage += (int)tdsValue;
  mainPage += " ppm</p>\n";

  mainPage += "<p>Collected "; // how old are values
  mainPage += epochTime - uploadedEpoch;
  mainPage += " seconds ago\n";

  if (debug)
  {
    mainPage += "<br>Collected epoch: ";
    mainPage += uploadedEpoch;
    mainPage += "</p>\n";
  }

  mainPage += "<p>Thingspeak upload "; // uploaded
  if (uploadSuccess)
  {
    mainPage += "successful";
  }
  else
  {
    mainPage += "failed";
  }
  mainPage += "</p>\n";

  mainPage += "<p>Pumps are "; // uploaded
  if (relayState)
  {
    mainPage += "enabled\n";
    mainPage += "<br><a href=\"/toggleRelay\">Disable pumps</a>\n";
  }
  else
  {
    mainPage += "disabled";
    mainPage += "<br><a href=\"/toggleRelay\">Enable pumps</a>\n";
  }
  mainPage += "</p>\n";

  mainPage += "<p><FORM>\n";
  mainPage += "<INPUT TYPE=\"button\" onClick=\"history.go(0)\" VALUE=\"Refresh page\">\n";
  mainPage += "</FORM></p>\n";

  mainPage += "</div>\n";
  mainPage += "</body>\n";
  mainPage += "</html>\n";
  return mainPage;
}

void decodeMessage(String message)
{
  message.trim();

  if (debug)
    Serial.println();
  if (debug)
    Serial.print("Message as String: ");
  if (debug)
    Serial.print(message);
  if (debug)
    Serial.println();
  if (debug)
    Serial.print("String length: ");
  if (debug)
    Serial.println(message.length());

  boolean validData = 1;

  if (message.indexOf("Temp:") >= 0 && message.indexOf("pH:") >= 0 && message.indexOf("TDS:") >= 0)
  {

    if (debug)
      if (debug)
        Serial.println("Message has data");
    int str_len = message.length() + 1; // length (with one extra character for the null terminator)
    char char_array[str_len];           // prepare the character array (the buffer)

    message.toCharArray(char_array, str_len); // copy it over to array buffer

    if (debug)
      Serial.print("Message as char array: ");
    if (debug)
      Serial.print(char_array);
    if (debug)
      Serial.println();

    int i;
    char delimiter[] = ",";
    char *p;
    String words[3];

    i = 0;
    p = strtok(char_array, delimiter);
    while (p && i < 3)
    {
      words[i] = p;
      p = strtok(NULL, delimiter);
      ++i;
    }

    for (i = 0; i < 3; ++i)
    {
      if (words[i].indexOf("Temp:") >= 0)
      {
        if (debug)
          Serial.println("Found temperature");
        words[i].remove(0, 5);
        temperatureSum = words[i].toFloat();
        Serial.print("Temp: ");
        if (temperatureSum)
        {
          Serial.println(temperatureSum);
        }
        else
        {
          validData = 0;
          Serial.println("NA");
        }
      }
      else if (words[i].indexOf("pH:") >= 0)
      {
        if (debug)
          Serial.println("Found pH");
        words[i].remove(0, 3);
        pHValue = words[i].toFloat();
        Serial.print("pH: ");
        if (pHValue)
        {
          Serial.println(pHValue);
        }
        else
        {
          validData = 0;
          Serial.println("NA");
        }
      }
      else if (words[i].indexOf("TDS:") >= 0)
      {
        if (debug)
          Serial.println("Found TDS");
        words[i].remove(0, 4);
        tdsValue = words[i].toFloat();
        Serial.print("TDS: ");
        if (tdsValue)
        {
          Serial.println(tdsValue);
        }
        else
        {
          validData = 0;
          Serial.println("NA");
        }
      }
    }

    if (validData)
    {
      if (debug)
        Serial.println("Uploading data to thingspeak...");

      ThingSpeak.setField(1, temperatureSum);
      ThingSpeak.setField(2, pHValue);
      ThingSpeak.setField(3, tdsValue);

      int x = ThingSpeak.writeFields(myChannelNumber, myWriteAPIKey); // write to the ThingSpeak channel

      if (x == 200)
      {
        Serial.println("Thingspeak channel update successful.");
        uploadSuccess = 1;
      }
      else
      {
        Serial.println("Problem updating thingspeak channel. HTTP error code " + String(x));
        uploadSuccess = 0;
      }

      timeClient.update();

      uploadedEpoch = timeClient.getEpochTime();

      if (debug)
        Serial.println("Uploading data to thingspeak...");

      Blynk.virtualWrite(V0, temperatureSum);
      Blynk.virtualWrite(V1, pHValue);
      Blynk.virtualWrite(V2, tdsValue);
    }
    else
    {
      Serial.println("Message did not contain valid data");
    }
  }
  else if (message == "i")
  {
    Serial.print("IP: ");
    Serial.println(WiFi.localIP());
  }
  else if (message == "m")
  {
    Serial.print("MAC: ");
    Serial.println(WiFi.macAddress());
  }
  else if (message == "d")
  {
    if (debug)
    {
      debug = 0;
      Serial.println("Debug disabled");
    }
    else
    {
      debug = 1;
      Serial.println("Debug enabled");
    }
  }
  else
  {
    Serial.println("Message is not valid");
  }

  if (debug)
    Serial.println();
}

#ifdef DODEBUG
const char *wifi_status_to_string(wl_status_t status)
{
  /*
    typedef enum {
    WL_NO_SHIELD        = 255,   // for compatibility with WiFi Shield library
    WL_IDLE_STATUS      = 0,
    WL_NO_SSID_AVAIL    = 1,
    WL_SCAN_COMPLETED   = 2,
    WL_CONNECTED        = 3,
    WL_CONNECT_FAILED   = 4,
    WL_CONNECTION_LOST  = 5,
    WL_DISCONNECTED     = 6
} wl_status_t;
*/

  switch (status)
  {
  case WL_NO_SHIELD:
    return "WL_NO_SHIELD";
  case WL_IDLE_STATUS:
    return "WL_IDLE_STATUS";
  case WL_NO_SSID_AVAIL:
    return "WL_NO_SSID_AVAIL";
  case WL_SCAN_COMPLETED:
    return "WL_SCAN_COMPLETED";
  case WL_CONNECTED:
    return "WL_CONNECTED";
  case WL_CONNECT_FAILED:
    return "WL_CONNECT_FAILED";
  case WL_CONNECTION_LOST:
    return "WL_CONNECTION_LOST";
  case WL_DISCONNECTED:
    return "WL_DISCONNECTED";
  default:
    return "NA";
  }
}

// const char *wifi_station_get_connect_status_to_string(station_status_t status)
const char *wifi_station_get_connect_status_to_string(int status)
{
  /*
    typedef enum {
    STATION_IDLE = 0,
    STATION_CONNECTING,
    STATION_WRONG_PASSWORD,
    STATION_NO_AP_FOUND,
    STATION_CONNECT_FAIL,
    STATION_GOT_IP
} station_status_t;
*/

  /*
  switch (status)
  {
  case STATION_GOT_IP:
    return "STATION_GOT_IP";
  case STATION_NO_AP_FOUND:
    return "STATION_NO_AP_FOUND";
  case STATION_CONNECT_FAIL:
    return "STATION_CONNECT_FAIL";
  case STATION_WRONG_PASSWORD:
    return "STATION_WRONG_PASSWORD";
  case STATION_IDLE:
    return "STATION_IDLE";
  case WL_DISCONNECTED:
    return "WL_DISCONNECTED";
  default:
    return "NA";
  }
*/

  switch (status)
  {

  case 0:
    return "STATION_IDLE";
  case 1:
    return "STATION_CONNECTING";
  case 2:
    return "STATION_WRONG_PASSWORD";
  case 3:
    return "STATION_NO_AP_FOUND";
  case 4:
    return "STATION_CONNECT_FAIL";
  case 5:
    return "STATION_GOT_IP";
  default:
    return "NA";
  }
}
#endif

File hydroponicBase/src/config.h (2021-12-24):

String programName = "ardHydroponic";
String date = "20210417";
String author = "Jon Sagebrand";
String email = "jonsagebrand@gmail.com";

/**********
 * Debug and info
 **********/
bool debug = 0;      // output all debugging info
const byte info = 0; // 0: no info; 1: plotting, all values with headers on one line; 2: header and value on separate lines

/**********
 * Configurable variables
 **********/
char *varNames[] = {
    // This is the text printed on the LCD in 'Settings' mode
    "Nutr pump time,   ms", /* 0 */
    "pH+ pump time,    ms", /* 1 */
    "pH- pump time,    ms", /* 2 */
    "Clean pumps time, ms", /* 3 */
    "Iteration time,   ms", /* 4 */
    "Stir time,        ms", /* 5 */
    "Stir interval,    ms", /* 6 */
    "pH low,           pH", /* 7 */
    "pH high,          pH", /* 8 */
    "TDS low,         ppm", /* 9 */
    "k value,    constant", /* 10 */
    "TDS factor, constant", /* 11 */
    "Neutral pH,       pH", /* 12 */
    "Acid pH,          pH", /* 13 */
    "Neutral voltage,  mV", /* 14 */
    "Acid voltage,     mV", /* 15 */
    "pH voltage offs., mV"  /* 16 */
};

float vars[] = {
    // initial values of the configurable variables
    500.00,   /* 0, Nutr pump time, ms */
    500.00,   /* 1, pH+ pump time, ms */
    500.00,   /* 2, pH- pump time, ms */
    30000.00, /* 3, Clean pumps time */
    10000.00, /* 4, Iteration time, ms */
    5000.00,  /* 5, Stir time, ms */
    15000.00, /* 6, Stir interval, ms */
    4.62,     /* 7, pH low, pH */
    4.63,     /* 8, pH high, pH */
    800.00,   /* 9, TDS low, ppm */
    1.08,     /* 10, k value, factor */
    1.0,      /* 11, TDS factor, factor */
    7.0,      /* 12, Neutral pH, pH */
    4.0,      /* 13, Acid pH, pH */
    1500.0,   /* 14, Neutral voltage, mV */
    2032.44,  /* 15, Acid voltage, mV */
    1500.0    /* 16, pH voltage offset, mV */
};

float incs[] = {
    // increments/decrements when pushing buttons 4 and 5 in 'Settings'
    100.00,  /* 0, Nutr pump time, ms */
    100.00,  /* 1, pH+ pump time, ms */
    100.00,  /* 2, pH- pump time, ms */
    1000.00, /* 3, Clean pumps time */
    1000.00, /* 4, Iteration time, ms */
    1000.00, /* 5, Stir time, ms */
    1000.00, /* 6, Stir interval, ms */
    0.01,    /* 7, pH low, pH */
    0.01,    /* 8, pH high, pH */
    1.00,    /* 9, TDS low, ppm */
    0.01,    /* 10, k value, factor */
    0.1,     /* 11, TDS factor, factor */
    0.1,     /* 12, Neutral pH, pH */
    0.1,     /* 13, Acid pH, pH */
    1.0,     /* 14, Neutral voltage, mV */
    1.0,     /* 15, Acid voltage, mV */
    1.0      /* 16, pH voltage offset, mV */
};

const int noOfVars = 17; // this must correlate to the above variables

/**********
 * Pins
 **********/
// LCD pins
//        Uno   Mega
// SDA -> A4    D20
// SCL -> A5    D21

const int pHPlusPump = 2;  // PH+ pump
const int pHMinusPump = 3; // PH- pump
const int nutrAPump = 4;   // nutrition A pump
const int nutrBPump = 5;   // nutrition B pump
const int stirrer = 6;

const int pHSensorPin = A0; // pH-sensor probe
const int ECSensorPin = A1; // ec/EC sensor
const int DS18S20Pin = A2;  // one wire pin

const int button1 = 7; // if you are using buttons, connect these
const int button2 = 8;
const int button3 = 9;
const int button4 = 10;
const int button5 = 11;

const int espHardwareReset = 12;
// connect ESP-Rx -> D18, ESP-Tx -> D19

const int resetPin = 14; // resets the Mega itself

/**********
 * EEPROM
 **********/
#include <EEPROM.h>

byte varNumber = 0;
byte oldVarNumber = 0;

const byte addressMultiplicator = 4; // we store all variables as floats which uses 4 bytes

/***********
 * Serial
 ***********/
const int serialBaudRate = 9600;

/**********
 * Debouncing
 **********/
#include <FTDebouncer.h> // load library for debouncing buttons
FTDebouncer pinDebouncer(30);

/***********
 * One Wire, DS18B20
 ***********/
#include <OneWire.h>
OneWire ds(DS18S20Pin); // creating a OneWire object

float temperatureSum; // average of all samples taken from one temp test
float oldTemperatureSum = 0;

byte data[12]; // variable to temporary hold readings
byte addr[8];  // variable to temporary hold the memory address of the readings

/**********
 * STD
 **********/
#include <stdlib.h>

/**********
 * LCD
 **********/
#include <LiquidCrystal_I2C.h>                          // Library for LCD
LiquidCrystal_I2C lcd = LiquidCrystal_I2C(0x27, 20, 4); // change to (0x27, 20, 4) for 20x4 LCD

/**********
 * EC/TDS sensor
 **********/
float voltage;
// float ecValue;   //before temperature compensation
float ecValue25; // after temperature compensation
float tdsValue;

const float aref = 5.0;
const float adcRange = 1024.0;

float TDSValue;
float oldTDSValue = 0;

/**********
 * pH sensor
 **********/
float pHVoltage; // the voltage reading from analog pin
float slope;
float intercept;

float pHValue; // calculated pH reading
float oldpHValue = 0;
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

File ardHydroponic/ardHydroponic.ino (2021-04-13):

/**********
* Include files
**********/

#include "config.h"
#include "logging.h"
#include "LCD.h"
#include "outputs.h"
#include "read.h"
#include "misc.h"
#include "eeprom.h"
#include "specialMaint.h"
#include "buttons.h"

void setup()
{
  /***********
  * Serial
  ***********/
  Serial.begin(serialBaudRate); // serial baudrate

  /*******************************
  * Print start information
  *******************************/
  if (debug)
    Serial.println();
  if (debug)
    Serial.println(programName);
  if (debug)
    Serial.println(date);
  if (debug)
    Serial.print("by ");
  if (debug)
    Serial.println(author);
  if (debug)
    Serial.println(email);
  if (debug)
    Serial.println();

  /**********
  * LCD
  **********/
  if (debug)
    Serial.println("Starting LCD...");

  lcd.begin();
  if (debug)
    Serial.println();

  bootScreen(programName);
  bootScreen(date);

  /**********
  * EEPROM
  **********/
  //clearEEPROM();
  if (debug)
    Serial.println("Reading EEPROM...");
  bootScreen("Reading EEPROM...   ");

  initEEPROMCheck();
  if (debug)
    Serial.println();

  /**********
  * In/Outputs
  **********/
  if (debug)
    Serial.println("Starting In/Outputs...");
  bootScreen("Starting In/Outputs.");

  pinMode(pHPlusPump, OUTPUT);
  pinMode(pHMinusPump, OUTPUT);
  pinMode(nutrAPump, OUTPUT);
  pinMode(nutrBPump, OUTPUT);
  pinMode(stirrer, OUTPUT);

  pinMode(espHardwareReset, OUTPUT);

  digitalWrite(resetPin, HIGH); // set pin high before it's defined
  pinMode(resetPin, OUTPUT);

  if (debug)
    Serial.println();

  /**********
  * Setup FTDebouncer pins
  **********/
  if (debug)
    Serial.println("Setting up buttons...");
  bootScreen("Setting up buttons..");

  pinDebouncer.addPin(button1, LOW); // pin has external pull-down resistor
  pinDebouncer.addPin(button2, LOW);
  pinDebouncer.addPin(button3, LOW);
  pinDebouncer.addPin(button4, LOW);
  pinDebouncer.addPin(button5, LOW);

  pinDebouncer.init(); // initiate debounce

  if (debug)
    Serial.println();

  /**********
   * ESP-01
   **********/
  if (debug)
    Serial.println("Starting ESP-01...");
  bootScreen("Starting ESP-01...  ");

  digitalWrite(espHardwareReset, HIGH);
  if (debug)
    Serial.println();

  if (debug)
    Serial.println("Starting Serial1 for ESP communication...");
  bootScreen("Starting Serial1... ");

  Serial1.begin(serialBaudRate);
  if (debug)
    Serial.println();

  if (debug)
    Serial.println("Resetting ESP module...");
  bootScreen("Resetting ESP module");

  esp01HardwareReset();
  if (debug)
    Serial.println();

  /**********
  * Initiate screen
  **********/
  clearLCD();
  printNormal();
  readSensors();
}

void loop()
{
  currentMillis = millis();

  /**********
  * Read buttons
  **********/
  pinDebouncer.update();

  checkMode(); // check if mode has changed

  /**********
   * Count down on LCD
   **********/
  if (mode == 0)
  { // normal mode

    counter = (vars[4] - (currentMillis - readMillis)) / 1000;

    if ((counter != oldCounter) && (counter >= 0) && (counter <= readMillis / 1000))
    {
      printToLCD(17, 0, String(counter));
      printToLCD(17 + intLength(counter), 0, " ");

      /*
      if (counter <= 1)
      {
        if (debug) Serial.println("Powering EC sensor...");
        digitalWrite(ECPower, HIGH); // setting the power pin for EC sensor to high
      }
      */

      oldCounter = counter;
    }

    /**********
     * Upload data
     **********/
    if (currentMillis - readMillis > max(vars[0], max(vars[1], vars[2])) && newData)
    { // pumps has stopped
      mode = 2;
      checkMode();
      if (debug)
        Serial.println("Writing to Serial1...");
      writeToSerial1();
      //writeThingSpeak();
      mode = 0;
      checkMode();
      newData = 0;
    }

    /**********
    * Read loop
    **********/
    if (currentMillis - readMillis >= vars[4])
    { // read mode
      mode = 1;
      checkMode(); // check if mode has changed

      readSensors();

      mode = 0;    // go back to normal mode
      checkMode(); // check if mode has changed

      readMillis = millis();
    }

    /**********
    * Stirrer
    **********/
    if (currentMillis - stirStopMillis >= vars[6] && !digitalRead(stirrer))
    { // time to stir
      startStirrer();
      stirStartMillis = currentMillis;
    }

    checkOutputStop(); // check if it's time to stop the pumps or stirrer
  }
  else if (mode == 3)
  {                   // maintenance mode
    checkMaintStop(); // check if pumps are running and if it's time to stop any of them
  }
  else if (mode == 5)
  {
    doSpecialMaint();
  }

  if (button1PushMillis != 0 && currentMillis - button1PushMillis >= longPushTime)
  {
    button1PushMillis = 0;
    longPush = 1;
    longPushButton1();
  }
}

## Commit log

2021-03-13 rotary encoder
2021-03-13 maint pump select
2021-03-14 maint pump starts
2021-03-15 started with buttons section
2021-03-15 exclude libraries, button long push
2021-03-20 new pins, schematics
    [ardHydroponic.kicad_pcb, ardHydroponic.sch]
2021-03-23 board layout
2021-03-23 deleted pcb
    [ardHydroponic_my_routes.kicad_pcb]
2021-03-24 bug, changed to float, settings partially implemen
    [buttons.h, config.h, read.h]
2021-03-24 new schematics
    [ardHydroponic.kicad_pcb, ardHydroponic.sch]
2021-03-24 new PCB
    [ardHydroponic.kicad_pcb]
2021-03-26 pH calibration, avarage readings
2021-04-05 kicad, programmer board
    [ardHydroponic.kicad_pcb, espProgrammerBoard.kicad_pcb, espProgrammerBoard.sch]
2021-04-05 text on copper
    [espProgrammerBoard.kicad_pcb]
2021-04-06 special, resets esp, clears EEPROM
    [ardHydroponic.ino, buttons.h, config.h]
2021-04-07 uploads when data is new and pumps has stopped
2021-04-07 special action to reset system
    [ardHydroponic.ino, buttons.h, config.h]
2021-04-08 esp in schematics
    [ardHydroponic.sch]
2021-04-08 pcb layout
    [ardHydroponic.kicad_pcb]
2021-04-11 blynk and webcontrol, relay output
2021-04-11 new board layout
    [ardHydroponic.kicad_pcb]
2021-04-13 added jumper
    [ardHydroponic.sch]
2021-04-13 prints ip to LCD
2021-04-13 prints IP and MAC to LCD
2021-04-13 readme and pdf schematics
2021-04-15 trying to print out wifi_station_get...()
2022-05-13 programmer board
    [espProgrammerBoard.kicad_pcb, espProgrammerBoard.kicad_sch]
2025-04-28 kicad 8
    [ardHydroponic.kicad_pcb, ardHydroponic.kicad_sch]
